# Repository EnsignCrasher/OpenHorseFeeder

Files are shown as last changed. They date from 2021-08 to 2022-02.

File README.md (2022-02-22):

# OpenHorseFeeder

<p float="left" width="100%">
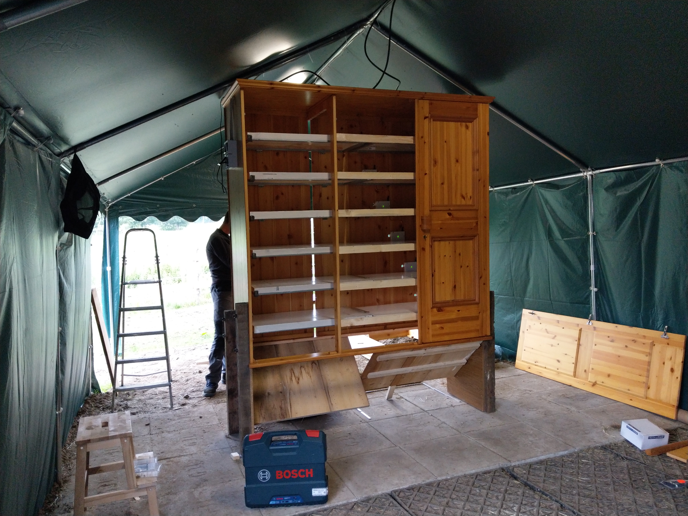
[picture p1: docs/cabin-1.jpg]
  
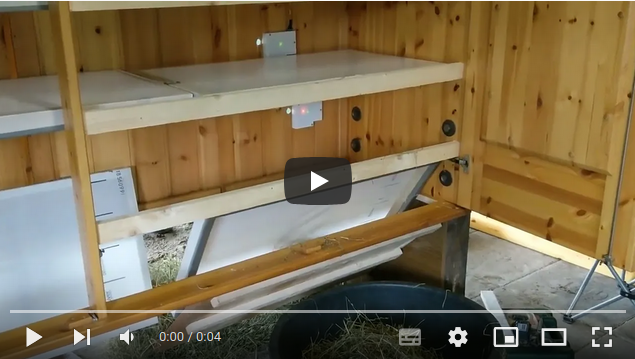
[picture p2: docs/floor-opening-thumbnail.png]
  
</p>

In general OpenHorseFeeder works by putting one portion of hay onto a floor
which is then released with an electric lock. It mostly depends on the size of
your cabin how many floors you can put in there.
For this one main module based on a Raspberry Pi Zero is used. Each electric
lock is then controlled by an Arduino Pro Mini which opens the lock and reports
the locks status to the main module with I2C.

> NOTE: Right now this approach isn't optimized for power consumption. If you are looking for a low power off-the-grid solution this
project may be interesting for you: https://github.com/EeroVakiparta/Feed-O-Pony

Parts needeed
=============

- 1x Raspberry Pi Zero W
- Network cable for module connection (or any other cable with at least 6 wires)
- [1x 12V power supply with barrel connector](https://www.amazon.de/-/en/LED-Power-Supply-12-24/dp/B07FNMKTBL/ref=sxin_13_b2b_sx_ftd_qd)
- [1x 5v-3.3V level shifter](https://www.amazon.de/RUNCCI-YUN-4-Channel-Converter-Bidirectional-Microcontroller/dp/B082F6BSB5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)
- [1x XL4015 Step-Down](https://www.amazon.de/-/en/XL4015-Converter-Module-1-25-36V-Adjustable/dp/B07XRF9NWP/ref=sr_1_6)
- [2 pairs per module: Multiplex connectors per module](https://www.amazon.de/10-Pairs-20-Pieces-Multiplex-Compatible-Trading/dp/B00ON2EXL8/ref=sr_1_2_sspa)
- [1 per module: Arduino Pro Mini](https://www.amazon.de/-/en/AZDelivery-PRO-Mini-ATmega328-16MHz/dp/B07VKLCYFV/ref=sr_1_3)
- [1 per module: IRFZ44N MOSFET](https://www.amazon.de/Youmile-Transistor-N-Channel-International-Rectifier/dp/B07QGNBJDF/ref=sr_1_3_sspa)
- [1 per module: electric lock](https://www.amazon.de/-/en/Electric-Electromagnetic-Locking-Cabinet-Emergency/dp/B07KWMH16C/ref=sr_1_9)

Electrics
=========
The main module uses an external 12V power supply. This will be used to drive
the 12V electric locks. For the Raspberry Pi and Arduinos a step-down converter
to 5V is build into the main module.

Modules Connectors
------------------
The connector cables are simply wired in parallel with a male input and a male
output connector. Therefore the modules have a female input and female output
connector. Because of the parallel wired connector cable the pinout for the
input and output connectors on the modules are mirrored.

Incoming                    |Outgoing
:--------------------------:|:---------------------------:
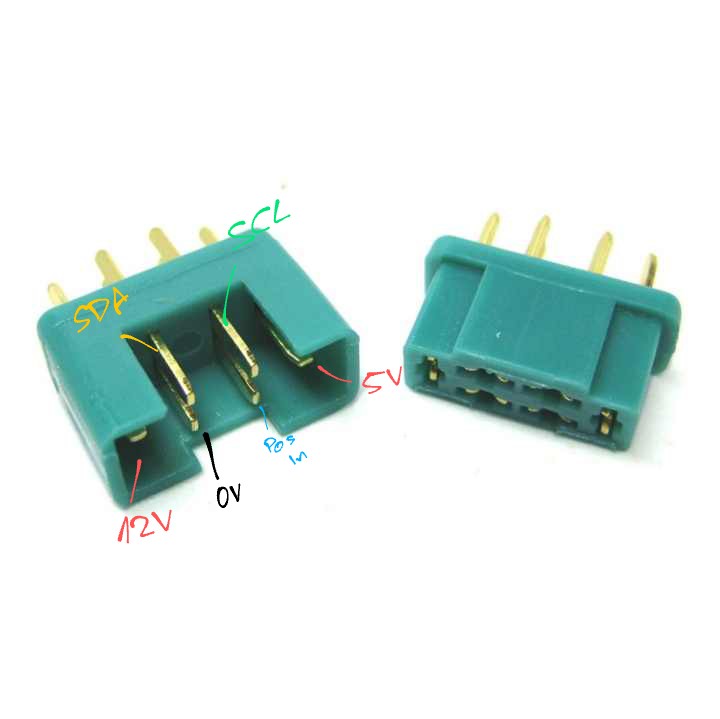
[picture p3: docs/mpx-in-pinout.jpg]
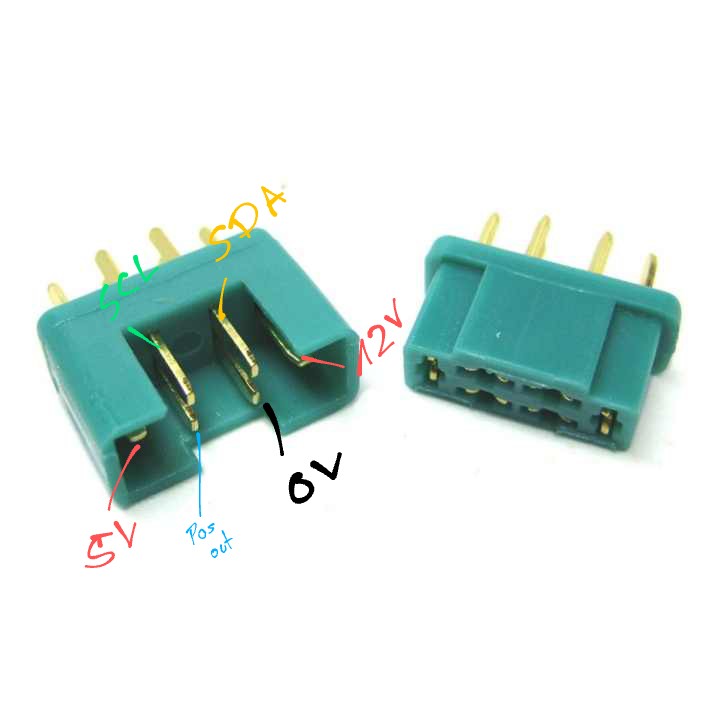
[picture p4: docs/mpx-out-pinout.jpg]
 | 

Main Module
===========

The Raspberry Pi uses 3.3V level for I2C and the Arduino uses 5V, therefore a
level shifter is needed to fix this.

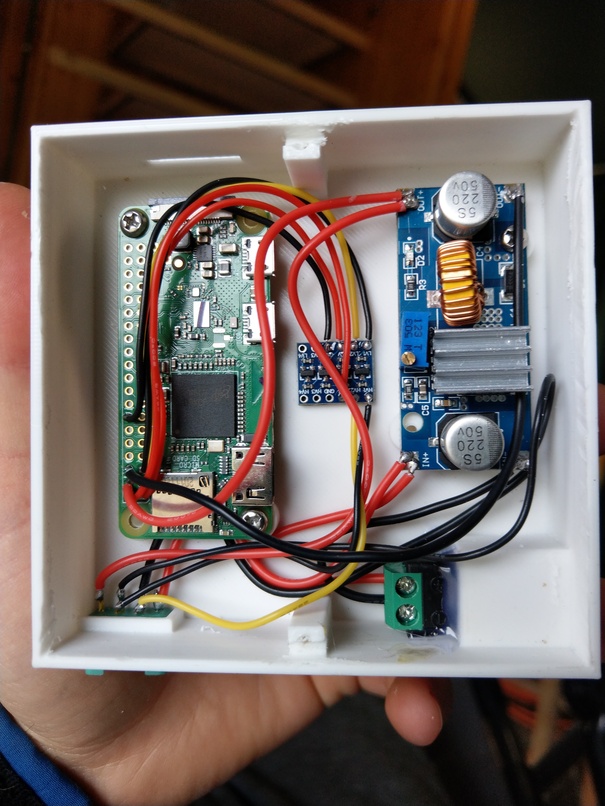
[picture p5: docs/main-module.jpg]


Floor Module
=============

The electric lock has a sensor which triggers when the hook is opened. This is
a simple switch connected to the green and white wire.

Also the module uses the serial interface to find it's position.
During initialization, the module will start at position 0 and print that on TX.
If the next modules recieves something on RX, it will increment that by one and
also write that to TX.
That way each module in the string can find out it's position with the first one
having the lowest position.

Wiring
------

Arduino pin|part
:---------:|:-------------:
10         |IFRZ44N Gate
2          |lock white wire (switch)
RX         |pos in
TX         |pos out
SCL        |SCL
SDA        |SDA

Image                       |Wiring diagram
:--------------------------:|:---------------------------:
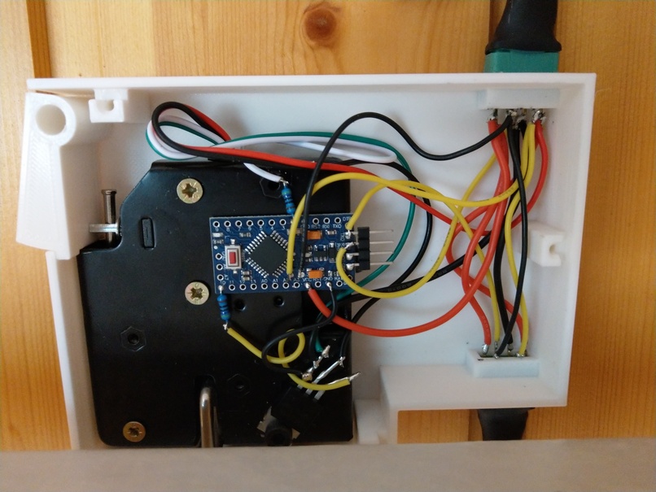
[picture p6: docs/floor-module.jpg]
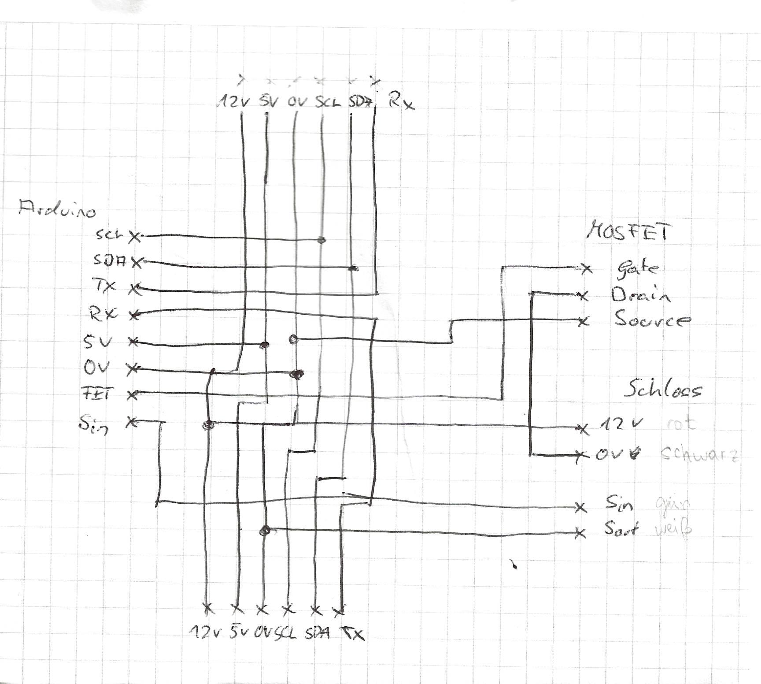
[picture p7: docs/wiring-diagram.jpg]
  | 

Flashing
--------

Nothing special here, just flash the code to the Pro Mini using your favourite
method (i.e. Arduino IDE). To do this connect the device's serial with your pc
with an USB-TTL converter. When you hit the upload button in the Arduino IDE and
it says "uploading..." in the log box at the bottom, you need to hit the reset
button real quick to make it work.

Make sure your module isn't connected to any already flashed module, as this
pollutes the serial communication.

After flashing you should be able to put the module into any location, as it
finds it's position in the string automatically.

Wire lengths for mass production
=================================

Floor module
------------

As long as there is no PCB for this modules, here is a list of all wires for
quick preparation:

Size (AWG)|Color |Total Length|Middle stripped part
:--------:|:----:|:----------:|:------------------:
22        |Red   |80mm        |-
22        |Red   |170mm       |72mm
22        |Black |170mm       |72mm
28        |Yellow|170mm       |72mm
28        |Black |170mm       |72mm
28        |Yellow|120mm       |-
28        |Yellow|120mm       |-
28        |Yellow|80mm        |-
28        |Black |80mm        |-

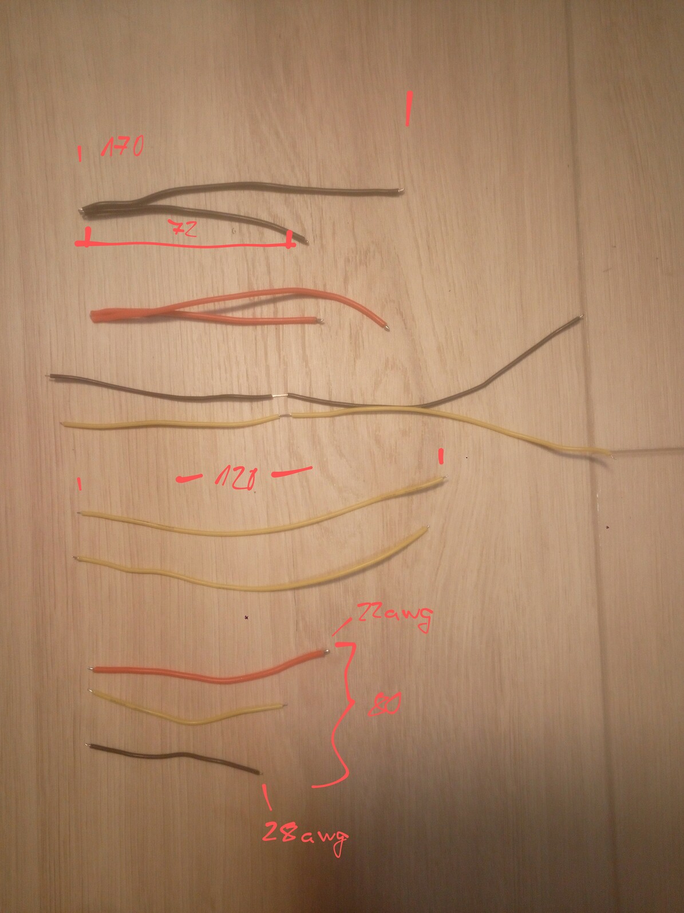
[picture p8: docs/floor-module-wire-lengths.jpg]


inter-module connections
------------------------

Usually you don't want your modules to be mounted in one line, as the floor from
above would hit the module underneath it. So your modules will usually be slightly
shifted at each floor.

To calculate the connection wire length according to the image below, you can
use this formula:

```
l = d - b + a
```

for a distance between the floors of 300mm it would be:

```
l = 300mm - 90mm + 120mm = 330mm
```

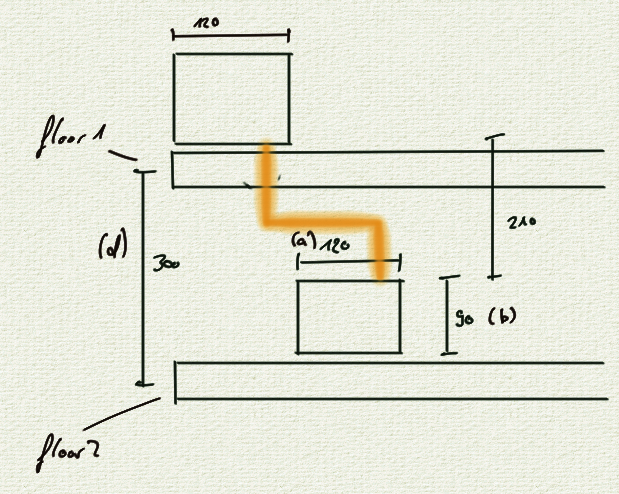
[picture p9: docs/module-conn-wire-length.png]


Future improvements
===================

Preparing cables with MPX connectors is a very labour intensive task, it maybe
be better to use network cables for this. It may be possible to use connectors
like [this](https://www.amazon.de/dp/B07G2BR8HQ/ref=cm_sw_r_apan_glt_i_02XD9R9ZNHF0BPCT05TW)
to build into the modules. Wiring this thing would be mostly done with a network
cable tool which is a lot quicker than stripping and soldering all the cables.

Also the wiring would be a lot less messy, you would simply connect the to plugs and then
the appropriate part in the module.

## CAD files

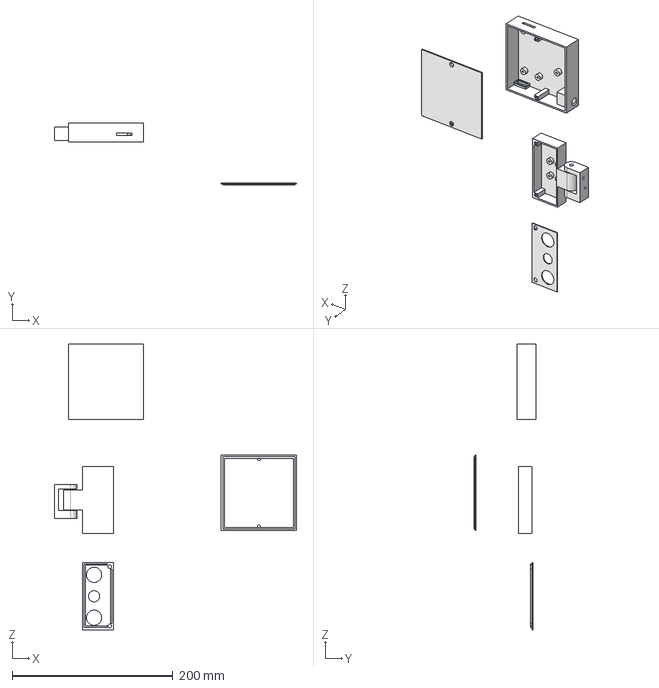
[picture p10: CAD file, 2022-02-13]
3dprint/main-module-and-rpi-cam.step
301.9 x 77.6 x 356.3 mm

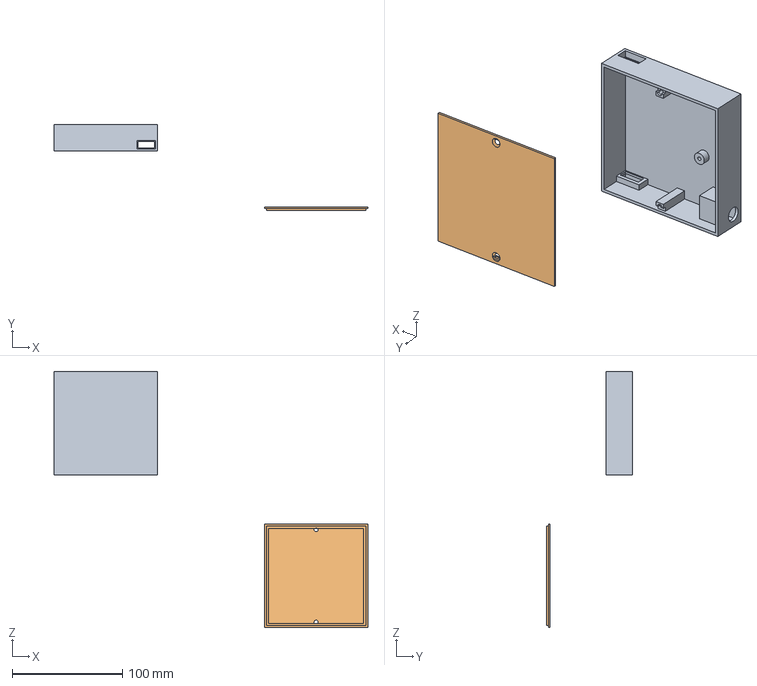
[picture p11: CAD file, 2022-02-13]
3dprint/main-module/main-module-rpi-external.step
284.6 x 77.6 x 232.4 mm

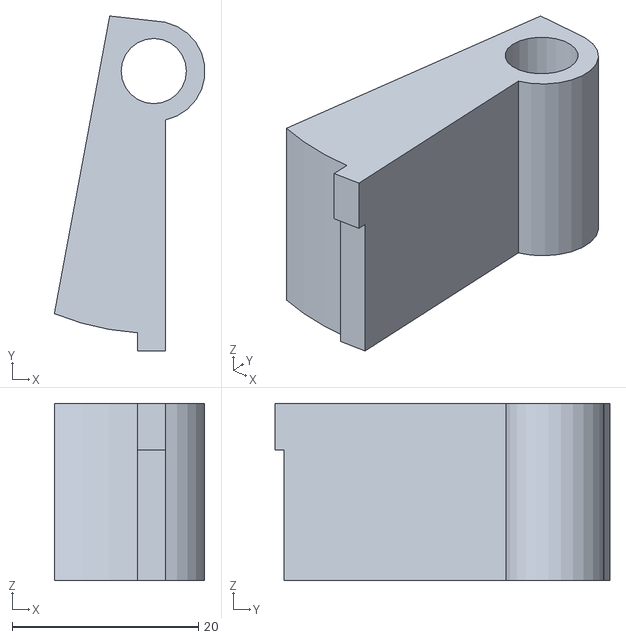
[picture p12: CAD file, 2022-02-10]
3dprint/floor-module/button.stl
16.1 x 36.0 x 19.0

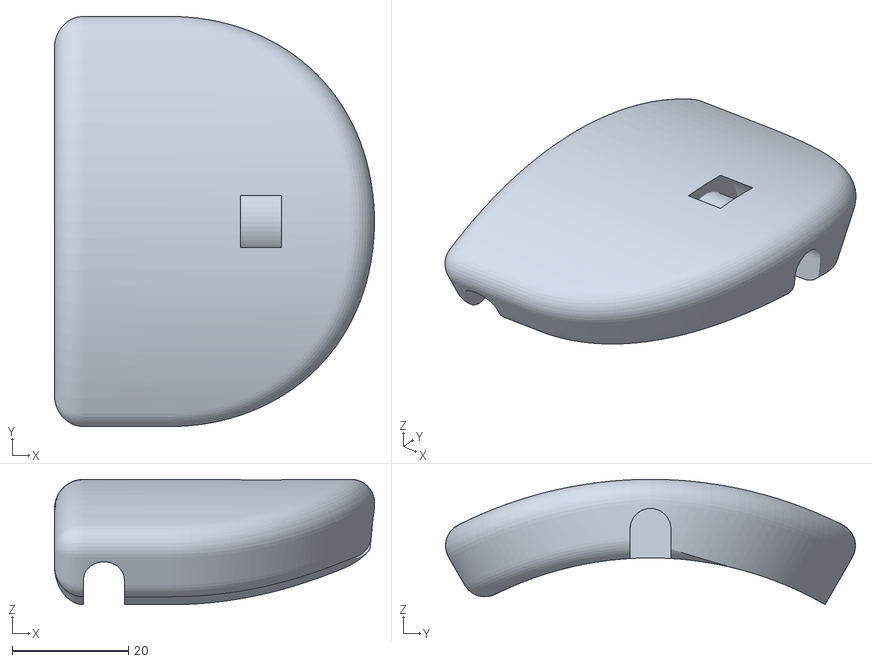
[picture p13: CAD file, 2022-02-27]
3dprint/horse-feeder-2-camera/v1-1-cage-cap.stl
55.0 x 70.5 x 21.5

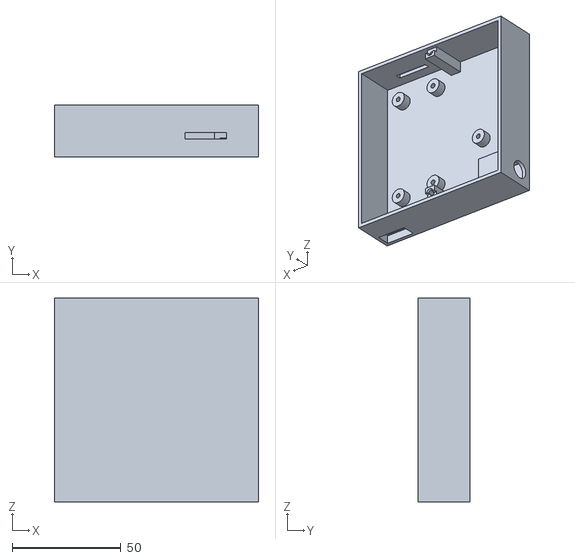
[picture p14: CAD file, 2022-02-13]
3dprint/main-module/case.stl
94.0 x 24.0 x 94.0

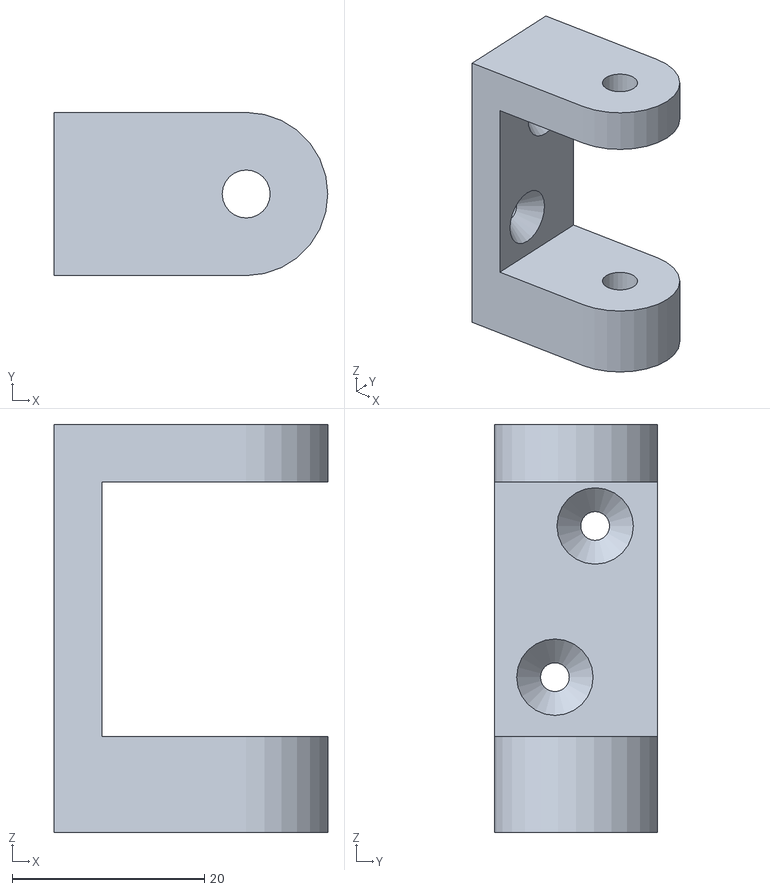
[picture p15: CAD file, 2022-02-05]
3dprint/rpi-camera-mount/case-mount.stl
28.5 x 17.0 x 42.5

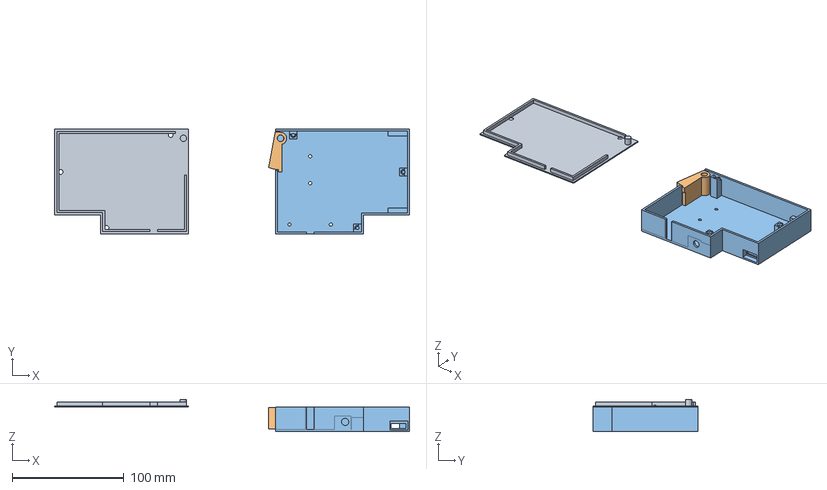
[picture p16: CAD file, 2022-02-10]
3dprint/floor-module.iges
317.3 x 94.0 x 29.0 mm

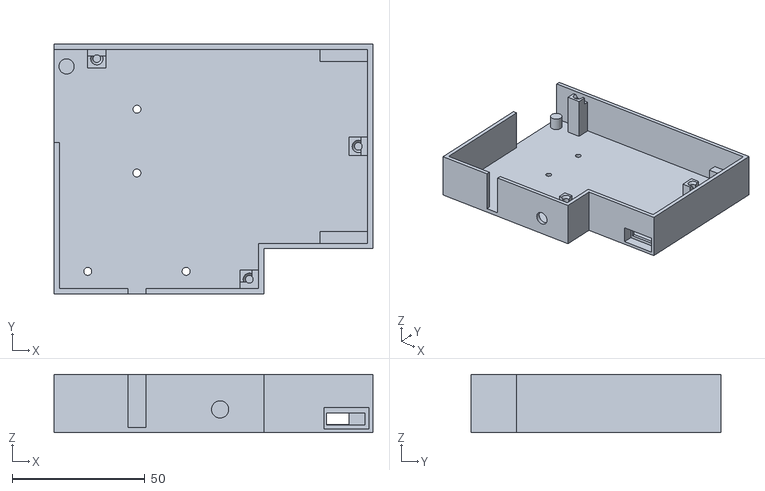
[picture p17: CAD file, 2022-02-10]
3dprint/floor-module/housing.stl
120.0 x 94.0 x 22.0

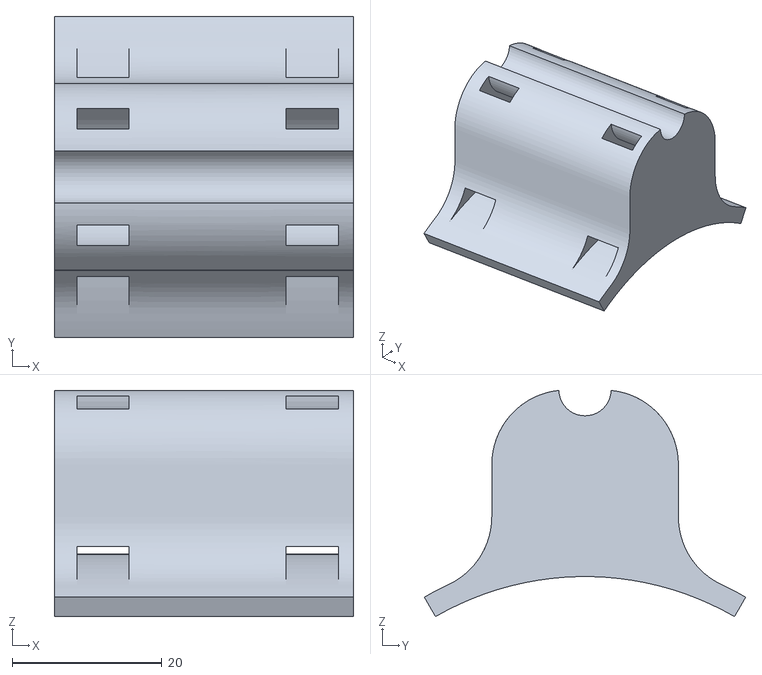
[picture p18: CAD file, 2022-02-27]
3dprint/horse-feeder-2-camera/v1-1-camera-mount.stl
40.0 x 43.0 x 30.3

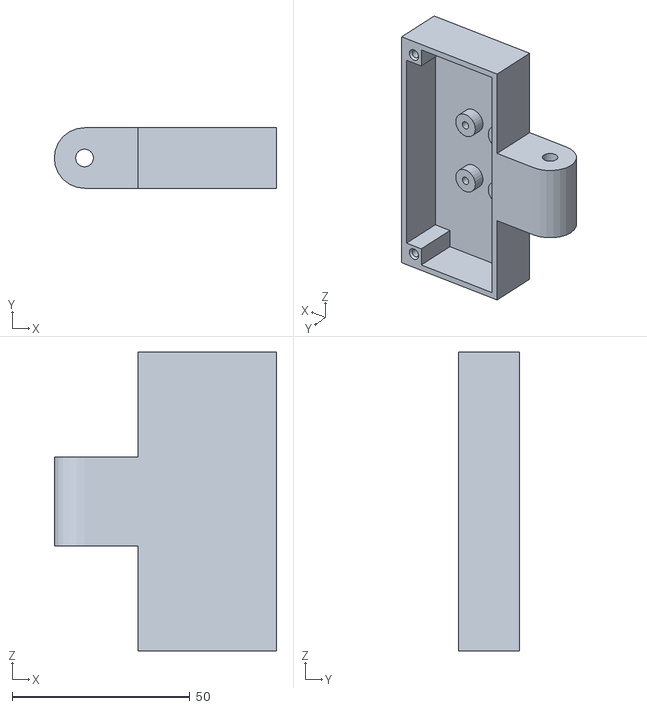
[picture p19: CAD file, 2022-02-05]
3dprint/rpi-camera-mount/case.stl
62.5 x 17.0 x 84.0

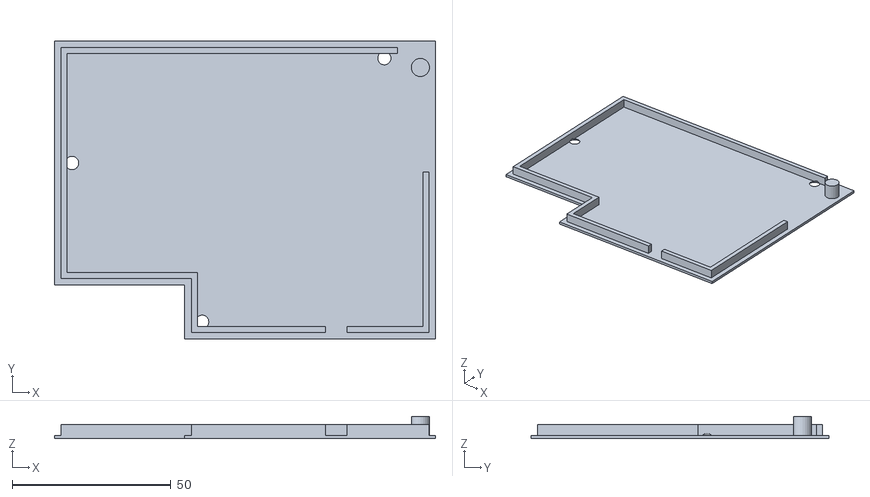
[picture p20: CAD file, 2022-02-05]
3dprint/floor-module/top.stl
120.0 x 94.0 x 6.96

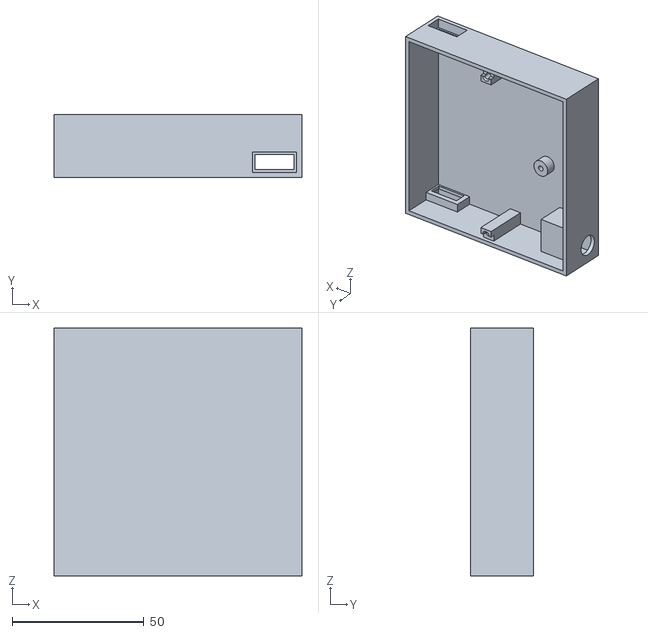
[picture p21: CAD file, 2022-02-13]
3dprint/main-module/case-rpi-external.stl
94.0 x 24.0 x 94.0

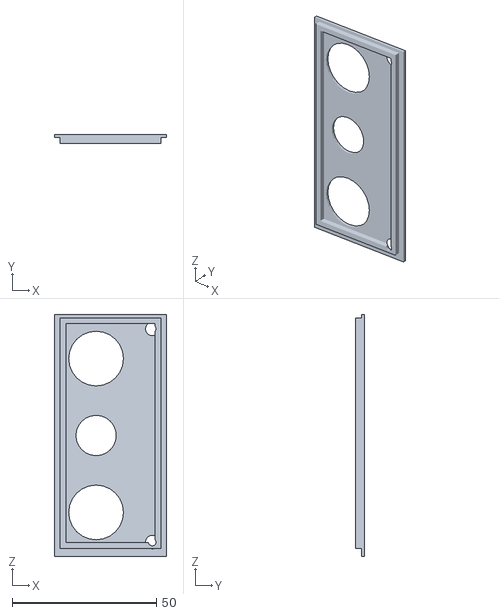
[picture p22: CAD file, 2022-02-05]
3dprint/rpi-camera-mount/lid.stl
39.0 x 2.95 x 84.0

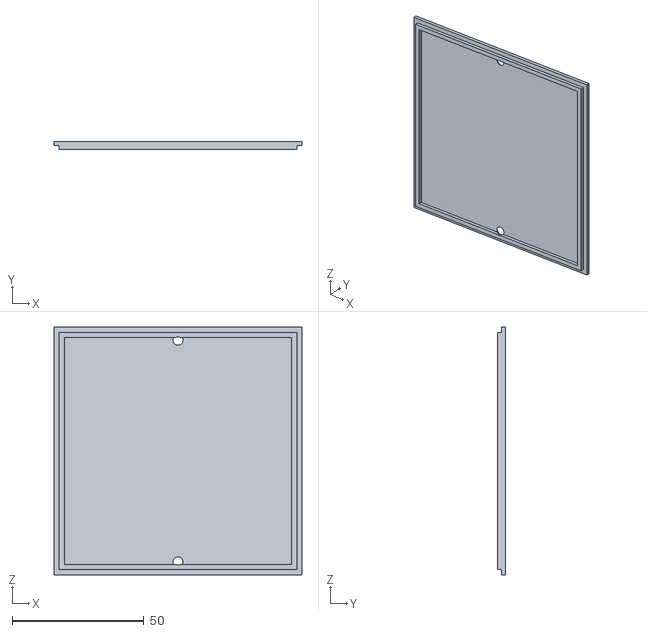
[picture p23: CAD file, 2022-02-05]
3dprint/main-module/lid.stl
94.0 x 3.00 x 94.0

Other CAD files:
3dprint/horse-feeder-2-camera/v1-1-rtp.f3d
3dprint/horse-feeder-2-camera/v1-1.f3d

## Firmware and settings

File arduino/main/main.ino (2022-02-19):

#include <string.h>
#include <stdlib.h>     /* atoi */


/*
  Arduino Slave for Raspberry Pi Master
  i2c_slave_ard.ino
  Connects to Raspberry Pi via I2C

  DroneBot Workshop 2019
  https://dronebotworkshop.com
*/
byte pos = 48;

void wait_for_address()
{
  byte new_pos = pos;
  while(millis() < 5000) {
    while(Serial.available()) {
      pos = Serial.read() + 1;
    }
    Serial.write(pos);
    delay(100);
  }
}

// Include the Wire library for I2C
#include <Wire.h>

uint64_t turn_off_ms = 0;
uint64_t turn_off_delay_ms = 3000;

const int ledPin = 13;
const int fetPin = 10;
const int btnPin = 2;

void setup() {
  Serial.begin(9600);

  // Setup pin 13 as output and turn LED off
  pinMode(ledPin, OUTPUT);
  pinMode(fetPin, OUTPUT);
  pinMode(btnPin, INPUT_PULLUP);
  for(int i=0; i<10; i++) {
    delay(50);
    digitalWrite(ledPin, HIGH);
    delay(50);
    digitalWrite(ledPin, LOW);
  }
  digitalWrite(fetPin, LOW);

  wait_for_address();

  Wire.begin(pos);

  // Call receiveEvent when data received
  Wire.onReceive(receiveEvent);
  Wire.onRequest(requestEvent);
}

// Function that executes whenever data is received from master
void receiveEvent(int howMany) {
  while (Wire.available()) { // loop through all but the last
    char c = Wire.read(); // receive byte as a character
    digitalWrite(fetPin, HIGH);
    digitalWrite(ledPin, HIGH);
    turn_off_ms = millis() + 3000;
  }
}

void requestEvent() {
  Wire.write(digitalRead(btnPin));
}

void loop() {
  if (turn_off_ms > 0 && millis() > turn_off_ms) {
    digitalWrite(fetPin, LOW);
    digitalWrite(ledPin, LOW);
    turn_off_ms = 0;
  }
  delay(100);
}

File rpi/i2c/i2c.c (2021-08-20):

#include <unistd.h>				//Needed for I2C port
#include <fcntl.h>				//Needed for I2C port
#include <sys/ioctl.h>			//Needed for I2C port
#include <linux/i2c-dev.h>		//Needed for I2C port
#include <stdio.h>
#include <stdlib.h>
#include <string.h>

int file_i2c;

int i2c_init(int addr) {
	char *filename = (char*)"/dev/i2c-1";
	if ((file_i2c = open(filename, O_RDWR)) < 0)
	{
		printf("Failed to open the i2c bus");
		return 1;
	}
	if (ioctl(file_i2c, I2C_SLAVE, addr) < 0)
	{
		printf("Failed to acquire bus access and/or talk to slave.\n");
		return 1;
	}
	return 0;
}

int i2c_read(int length, char *buffer) {
	//read() returns the number of bytes actually read, if it doesn't match
	//then an error occurred (e.g. no response from the device)
	int read_len=read(file_i2c, buffer, length);
	if (read_len != length)
	{
		printf("Failed to read from the i2c bus. Got %d bytes, wanted %d\n", read_len, length);
		return 1;
	}
	return 0;
}

int i2c_write(int length, char* buffer) {
	//write() returns the number of bytes actually written, if it doesn't
	//match then an error occurred (e.g. no response from the device)
	if (write(file_i2c, buffer, length) != length) {
		/* ERROR HANDLING: i2c transaction failed */
		printf("Failed to write to the i2c bus.\n");
		return 1;
	}
	return 0;
}

int usage() {
	printf("i2c: read write bytes to i2c devices\n\n");
	printf("\tget <addr DEC>\n\t\tread one byte from <addr>\n");
	printf("\tset <addr DEC> <value>\n\t\twrite byte <value> to <addr>\n");
	return 1;
}

int main(int argc, char* argv[]) {
	if (argc <= 1) return usage();

	if (0 == strcmp(argv[1], "get")) {
		if (argc <= 2) return usage();
		int addr = strtol(argv[2], NULL, 10);
		if(i2c_init(addr)) {
			return 1;
		}
		char value = 0;
		if(i2c_read(1, &value)) {
			return 1;
		}
		printf("%d\n", value);
	} else if (0 == strcmp(argv[1], "set")) {
		if (argc <= 3) return usage();

		int addr = strtol(argv[2], NULL, 10);
		if(i2c_init(addr)) {
			return 1;
		}

		int val = strtol(argv[3], NULL, 10);
		char cval = (char)val;
		if(i2c_write(1, &cval)) {
			return 1;
		}
	} else {
		printf("unknown mode %s\n", argv[1]);
		return 1;
	}
	return 0;
}

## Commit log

2021-08-20 first version which can toggle an led
2021-08-20 replace python with c++
    [i2c.c]
2021-08-20 rpi/i2c: add cli (get/set) + usage
2021-08-20 arduino: return led state on request
2021-08-20 arduino: actually toggle the relais
    if anything is received on i2c the module will be opened for 3 secs
    (according to the electric lock specs).
    the status will be read from btnPin whenever a request event comes in.
2021-08-20 arduino: implement auto-address for i2c
2021-08-20 arduino: blink led on startup
2021-08-20 rpi/i2c: not an easy task to code without any warning
2021-08-20 i2c: add i2cspeed for debugging
    there was some confusion about the i2c speed. This script can be used to show
    the currently used setting.
2021-08-20 rpi/feed: use installed i2c version
2021-10-09 docs: add wiring diagram
2022-02-05 3dprint: initial commit
    [button.stl, housing.stl, top.stl]
2022-02-05 3dprint: add remaining parts
    [case-mount.stl, case.stl, lid.stl]
2022-02-10 3dprint/floor-module: minor adjustments
    - increased diameter of button joint from 6mm to 7mm
    this way it should fit without needing to drill it
    - increased width of plug-cut-outs by 1mm
    [button.stl, housing.stl]
2022-02-10 3dprint: add models as .iges
    [floor-module.iges, main-module-and-rpi-cam.iges]
2022-02-12 docs: add info about floor module wire lengths
2022-02-13 3dprint/main-module: fix minor issues
    - multiplex connector is missing stop
    - lid screws are missing cut-outs
    - changed model format from iges to step
    [case.stl, main-module-and-rpi-cam.iges, main-module-and-rpi-cam.step]
2022-02-13 3dprint/main-module: add external rpi variant
    [case-rpi-external.stl, main-module-rpi-external.step]
2022-02-15 docs: inter-module wire length
2022-02-19 Arduino; make autopositioning work
2022-02-27 3dprint: add horse-feeder-2-camera parts
    [v1-1-cage-cap.stl, v1-1-camera-mount.stl, v1-1-rtp.f3d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]
2022-07-22 rpi/horse-feeder: retry i2c commands
    It seems like sometimes the i2c bus can be a bit flaky. To workaround
    this we will retry the i2c command a few times.
2022-08-25 debian: add packaging files for i2c and horse-feeder
